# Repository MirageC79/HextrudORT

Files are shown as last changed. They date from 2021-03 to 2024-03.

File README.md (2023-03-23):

# HextrudORT
Light, small and efficient extruder based on the popular Bondtech BMG.
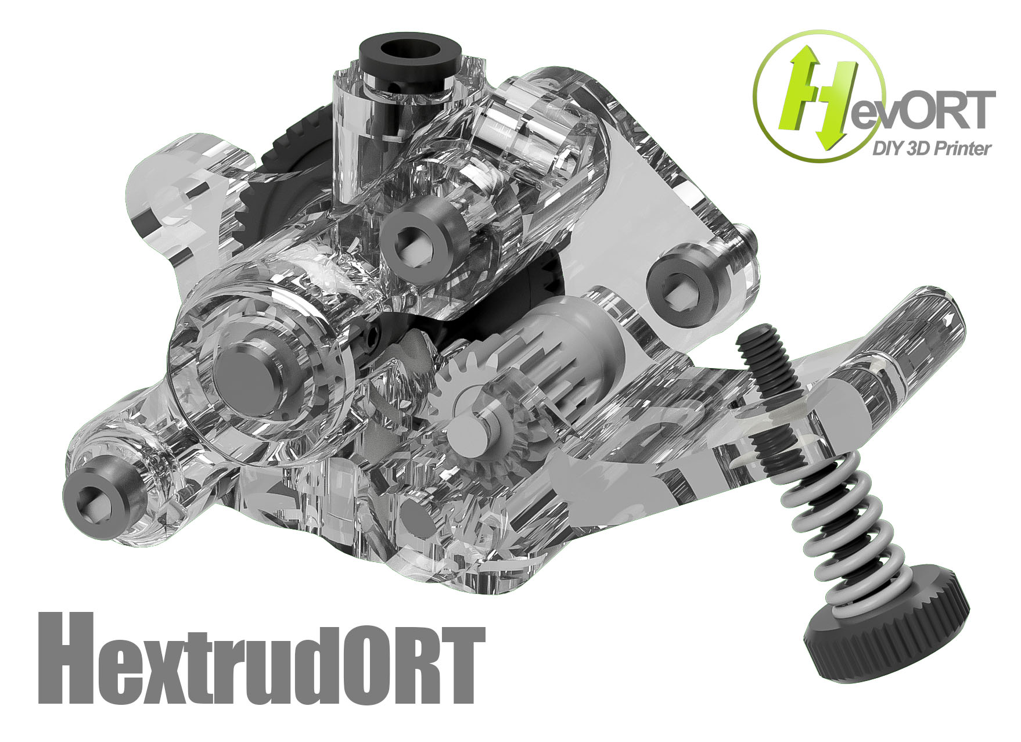
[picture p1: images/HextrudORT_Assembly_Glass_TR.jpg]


## Why the HextrudORT:
The HextrudORT is the simple combination of a proven concept and the desire to obtain a compact and lightweight print head for fast 3D printing.  
Re-using the internal components from the popular and efficient [Bondtech BMG](https://www.bondtech.se/en/product/bmg-extruder/){:target="_blank"}, this extruder was specifically designed to be merged into the [HevORT's](www.hevort.com) print head carriage.

<br>
<br>
<iframe width="200" height="150" src="https://www.youtube.com/embed/5HKC9tRqtTw" frameborder="0" allow="accelerometer; autoplay; clipboard-write; encrypted-media; gyroscope; picture-in-picture" allowfullscreen></iframe> <iframe width="200" height="150" src="https://www.youtube.com/embed/h-ukClHtai4" title="YouTube video player" frameborder="0" allow="accelerometer; autoplay; clipboard-write; encrypted-media; gyroscope; picture-in-picture" allowfullscreen></iframe> <iframe width="200" height="150" src="https://www.youtube.com/embed/YIFRRQczDmg" frameborder="0" allow="accelerometer; autoplay; clipboard-write; encrypted-media; gyroscope; picture-in-picture" allowfullscreen></iframe>

<br>

<br>
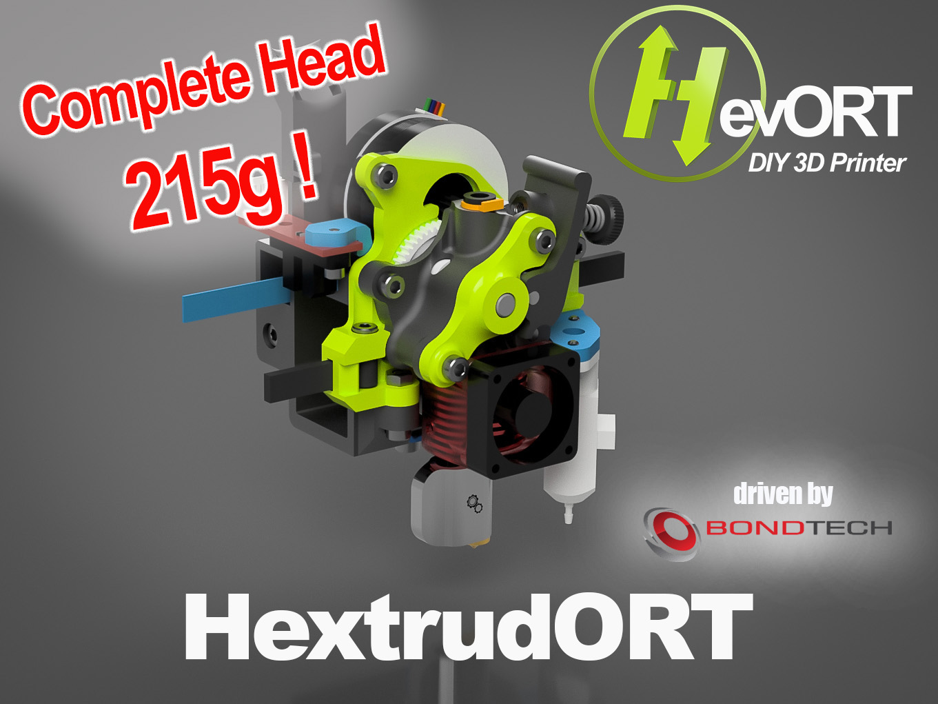
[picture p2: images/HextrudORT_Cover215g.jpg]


### Modular approach!
Several configurations can be created to support all HevORT XY gantry types as well as many populat HotEnds.  Select from the two tables here below your desired configuration and assemble them together :) 

### Change log: 
[Check here for change history:](https://github.com/MirageC79/HextrudORT/releases)

## Carriages

Item<br>Click for CAD|HevORT XY gantry to be used with|Data|Release Status
---------------------|--------------------------------|---|:------------:
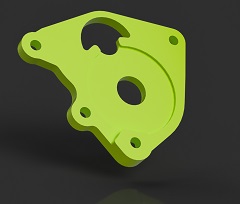
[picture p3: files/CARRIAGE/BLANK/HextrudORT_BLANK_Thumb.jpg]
Blank (https://a360.co/3tu2M2F)
{:target="_blank"}|*This is up to your imagination*|[STLs](https://www.thingiverse.com/thing:4796948){:target="_blank"} <br> <br> Merge this plate to your CAD in order install the Hextrudort|**RELEASED March 2021**
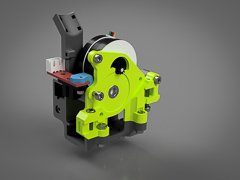
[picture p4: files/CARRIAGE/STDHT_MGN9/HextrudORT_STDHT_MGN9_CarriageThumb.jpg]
STDHTMGN9 (https://a360.co/3bJBDmp)
{:target="_blank"}|STD/HT MGN9|[STLs](https://www.thingiverse.com/thing:4793215){:target="_blank"} <br> <br> [BOM & Notes](/files/CARRIAGE/STDHT_MGN9/BOM_HextrudORT_Carriage_STDHT_MGN9.htm){:target="_blank"} <br> <br> [Excel](/files/CARRIAGE/STDHT_MGN9/BOM_HextrudORT_Carriage_STDHT_MGN9.xlsx)|**RELEASED March 2021**
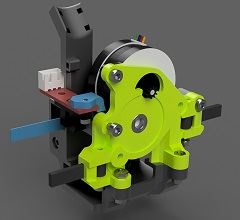
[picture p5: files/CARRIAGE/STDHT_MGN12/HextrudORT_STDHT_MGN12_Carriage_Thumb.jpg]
STDHTMGN12 (https://a360.co/3m0Uj4F)
{:target="_blank"}|STD/HT MGN12|[STLs](https://www.thingiverse.com/thing:4810748){:target="_blank"} <br> <br> [BOM & Notes](/files/CARRIAGE/STDHT_MGN12/BOM_HextrudORT_Carriage_STDHT_MGN12.htm){:target="_blank"} <br> <br> [Excel](/files/CARRIAGE/STDHT_MGN12/BOM_HextrudORT_Carriage_STDHT_MGN12.xlsx)|**RELEASED March 2021**
To come...|HD9|...|*est. April 2021*
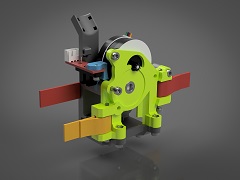
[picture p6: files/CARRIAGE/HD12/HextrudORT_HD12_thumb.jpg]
HD12 (https://a360.co/3bAL0EV)
{:target="_blank"}|HD12(MGN12)|[STLs](https://www.thingiverse.com/thing:4790412){:target="_blank"} <br> <br> [BOM & Notes](/files/CARRIAGE/HD12/BOM_HextrudORT_Carriage_HD12.htm){:target="_blank"} <br> <br> [Excel](/files/CARRIAGE/HD12/BOM_HextrudORT_Carriage_HD12.xlsx)|**RELEASED March 2021**

## Extruder & HotEnds Configs

Item<br>Click for CAD|HotEnd|Data|Release Status
---------------------|------|----|:------------:
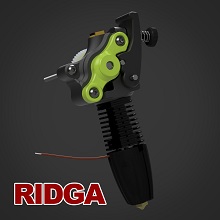
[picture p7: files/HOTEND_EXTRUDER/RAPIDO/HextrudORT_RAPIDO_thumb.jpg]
RAPIDO HotEnd (https://a360.co/3JzDvPC)
{:target="_blank"}|[RAPIDO & RAPIDO UHF](https://www.phaetus.com/rapido-plus/)|[STLs](https://github.com/MirageC79/HextrudORT/tree/main/files/HOTEND_EXTRUDER/RAPIDO/STLs){:target="_blank"} <br> <br> [BOM & Notes](/files/HOTEND_EXTRUDER/RAPIDO/BOM_HextrudORT_Extruder_Rapido.htm){:target="_blank"} <br> <br> [Excel](/files/HOTEND_EXTRUDER/RAPIDO/BOM_HextrudORT_Extruder_Rapido.xlsx)|**V1.65 March 2023**
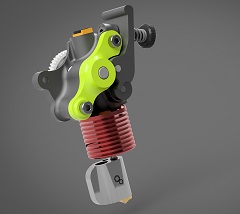
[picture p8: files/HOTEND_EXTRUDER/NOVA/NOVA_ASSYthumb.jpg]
NovaHotEnd (https://a360.co/3cmE7WT)
|[Nova HotEnd](https://3dpassion.com/nova)|[STLs](https://www.thingiverse.com/thing:4790773){:target="_blank"} <br> <br> [BOM & Notes](/files/HOTEND_EXTRUDER/NOVA/BOM_HextrudORT_Extruder_NOVA.htm){:target="_blank"} <br> <br> [Excel](/files/HOTEND_EXTRUDER/NOVA/BOM_HextrudORT_Extruder_NOVA.xlsx)|**RELEASED March 2021**
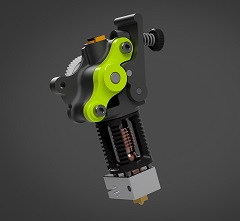
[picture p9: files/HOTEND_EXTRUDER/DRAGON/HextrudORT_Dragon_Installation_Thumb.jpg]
Dragon (https://a360.co/3tqIMhf)
{:target="_blank"}|[Dragon HotEnd](https://s.click.aliexpress.com/e/_AD0Qow)|[STLs](https://www.thingiverse.com/thing:4796562){:target="_blank"} <br> <br> [BOM & Notes](/files/HOTEND_EXTRUDER/DRAGON/BOM_HextrudORT_Extruder_Dragon.htm){:target="_blank"} <br> <br> [Excel](/files/HOTEND_EXTRUDER/DRAGON/BOM_HextrudORT_Extruder_Dragon.xlsx)|**RELEASED March 2021**
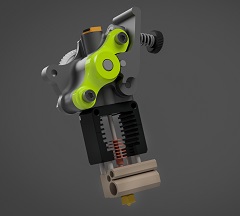
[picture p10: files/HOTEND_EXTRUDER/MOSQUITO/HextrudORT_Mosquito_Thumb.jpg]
Mosquito (https://a360.co/3tJ0A8Q)
{:target="_blank"}|[Mosquito HotEnd](https://www.sliceengineering.com/collections/mosquito-the-professional-hotend)|[STLs](https://www.thingiverse.com/thing:4965960){:target="_blank"} <br> <br> [BOM & Notes](/files/HOTEND_EXTRUDER/MOSQUITO/BOM_HextrudORT_Extruder_Mosquito.htm){:target="_blank"} <br> <br> [Excel](/files/HOTEND_EXTRUDER/MOSQUITO/BOM_HextrudORT_Extruder_Mosquito.xlsx)|**RELEASED September 2021**
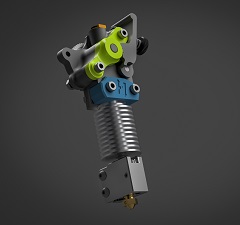
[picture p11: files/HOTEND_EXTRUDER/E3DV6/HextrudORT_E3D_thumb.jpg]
E3D V6 & Volcano (https://a360.co/3dGhSNx)
{:target="_blank"}|[E3D V6 & Volcano HotEnd](https://e3d-online.com/)|[STLs](https://www.thingiverse.com/thing:4971939){:target="_blank"} <br> <br> [BOM & Notes](/files/HOTEND_EXTRUDER/E3DV6/BOM_HextrudORT_Extruder_E3D.htm){:target="_blank"} <br> <br> [Excel](/files/HOTEND_EXTRUDER/E3DV6/BOM_HextrudORT_Extruder_E3D.xlsx)|**RELEASED September 2021**

<br>

## Report Issues [HERE](https://github.com/MirageC79/HextrudORT/issues)

<br>

## Back to [HevORT project](https://www.hevort.com)

<br>

**If you like my work** and would like to help me covering the costs associated to the development and improvement of this project, <br>
click the button here below :)

<form action="https://www.paypal.com/cgi-bin/webscr" method="post" target="_top">
<input type="hidden" name="cmd" value="_s-xclick" />
<input type="hidden" name="hosted_button_id" value="LYP98YKUSLXN2" />
<input type="image" src="https://www.paypalobjects.com/en_US/i/btn/btn_donateCC_LG.gif" border="0" name="submit" title="PayPal - The safer, easier way to pay online!" alt="Donate with PayPal button" />

</form>

Thank you!
Olivier

FB (https://www.facebook.com/groups/hevort) FaceBook Group <br>
forum (https://forums.hevort.com/index.php)  Discussion Forum <br>
Discord (https://discord.gg/WgZMrFSp) Discord Server <br>

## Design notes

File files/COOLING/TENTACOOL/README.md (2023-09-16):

# TentaCool
*design by sillisam71  
idea by MirageC*

## What if we are using CPAP turbine wrong?
I mean this thing is capable of decent pressure levels while still moving great amount of air...
And yet we are designing ducts with as little restriction as possible in order to get the maximum flow to the output nozzles.  

## Hypothesis:
Would an hybrid between berdair and regular ducting be something that would be better suited for that monster turbine?  More turbulent flow, more output holes and diffusers... see my point...   
What if we could create a carpet of turbulent air around the last layer?

TentaCool Pressure testing (https://www.youtube.com/watch?v=26Ztry5WomM)

Special thanks to *sillysam71* from the [HevORT discord server](https://discord.gg/4kxH2He3ab)  for this AMAZING creation based on my unclear and foggy explanations...
<br>
<br>

## Compatibility
- HextrudORT HD12 MGN9
  - Volcano
  - Rapido
  - Rapido UHF
  - CHC Volcano
- VZ PrintHead for HevORT (All HDs)
  - Goliath Short (Watercooled Extruder)
  - Pretty much any other hotend
    
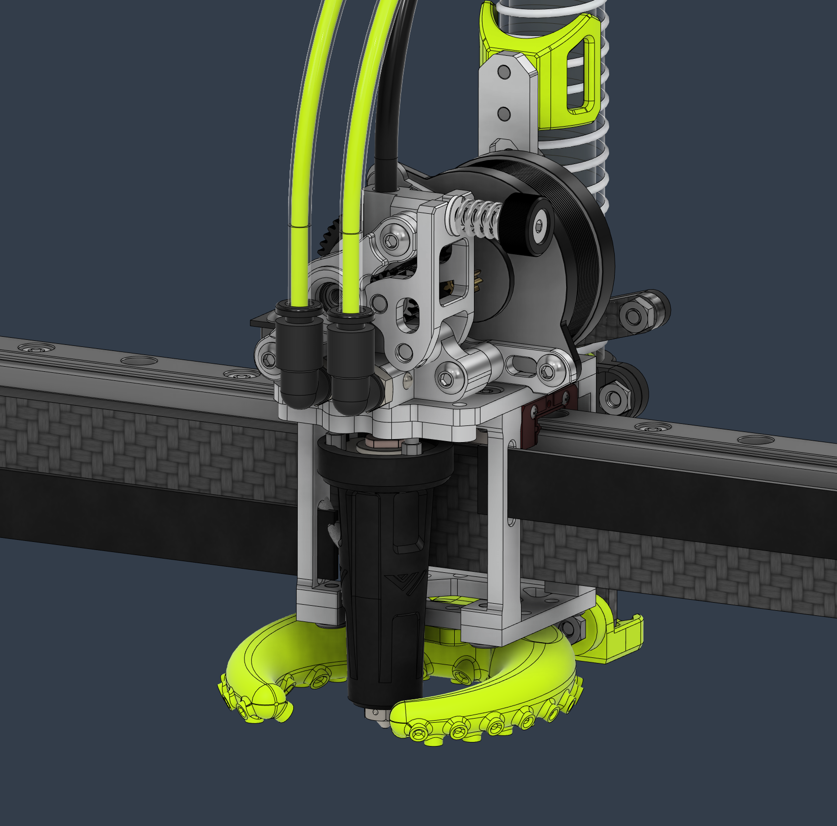
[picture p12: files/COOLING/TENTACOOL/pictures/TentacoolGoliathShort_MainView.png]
TentaCool VzPrintHead Goliath Short

tentacool_HD12_MGN9 Install
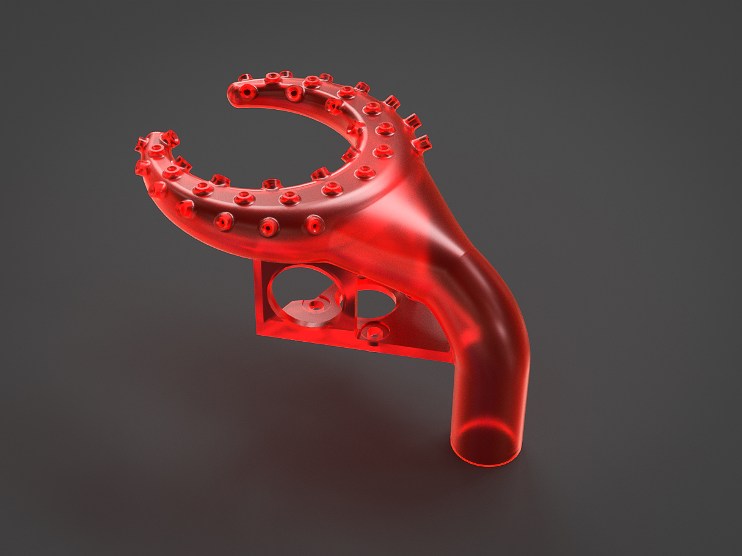
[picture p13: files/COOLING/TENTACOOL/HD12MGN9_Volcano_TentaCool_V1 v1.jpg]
TentaCool Duct


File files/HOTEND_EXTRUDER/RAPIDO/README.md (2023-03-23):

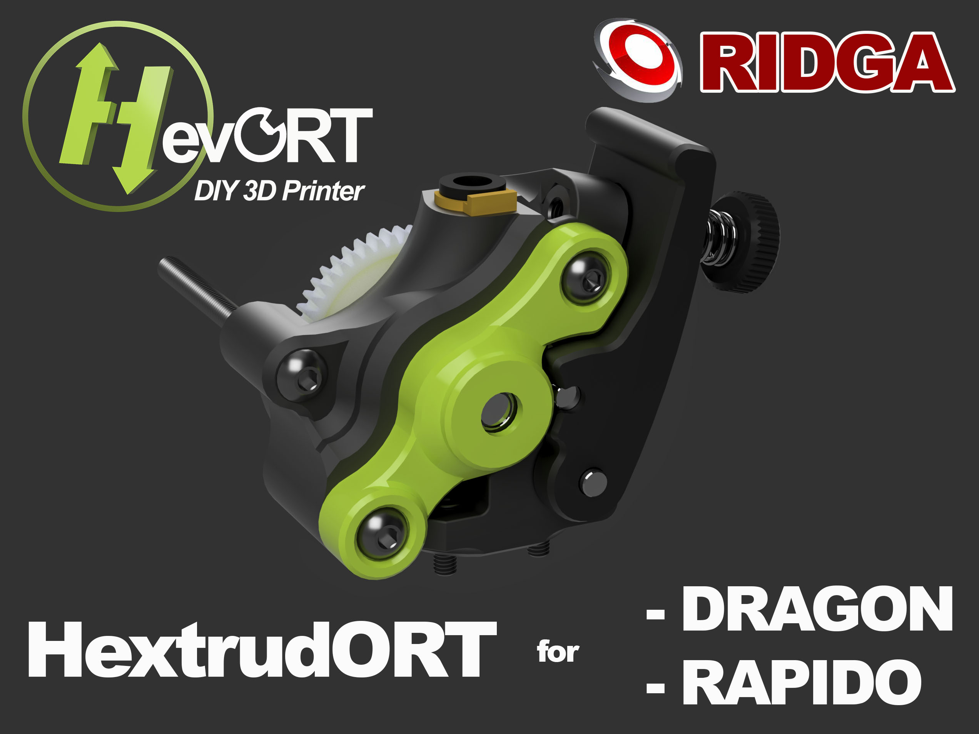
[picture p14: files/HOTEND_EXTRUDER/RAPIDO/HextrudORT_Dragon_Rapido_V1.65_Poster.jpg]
rapido


# [- CAD](https://a360.co/3JzDvPC) #
# [- BOM](https://miragec79.github.io/HextrudORT/files/HOTEND_EXTRUDER/RAPIDO/BOM_HextrudORT_Extruder_Rapido.htm) #

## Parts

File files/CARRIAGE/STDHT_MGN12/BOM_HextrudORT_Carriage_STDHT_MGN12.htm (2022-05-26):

SubAssy | Category | Item | Thumbnail | Part Name | Part Description | Make/Buy | QTY | Comment | Vendor | Vendor URL
HextrudORT Carriage_STDHT_MGN9 | BUY | 1
HextrudORT Carriage_STDHT_MGN9 | BUY | 1
HextrudORT Carriage_STDHT_MGN9 | BUY | 2
HextrudORT Carriage_STDHT_MGN9 | BUY | 3
HextrudORT Carriage_STDHT_MGN9 | HARDWARE | 4
HextrudORT Carriage_STDHT_MGN9 | HARDWARE | 6
HextrudORT Carriage_STDHT_MGN9 | HARDWARE | 17
HextrudORT Carriage_STDHT_MGN9 | HARDWARE | 18
HextrudORT Carriage_STDHT_MGN9 | HARDWARE | 19
HextrudORT Carriage_STDHT_MGN9 | HARDWARE | 20
HextrudORT Carriage_STDHT_MGN9 | HARDWARE | 21
HextrudORT Carriage_STDHT_MGN9 | HARDWARE | 22
HextrudORT Carriage_STDHT_MGN9 | HARDWARE | 23
HextrudORT Carriage_STDHT_MGN9 | MAKE | 27
HextrudORT Carriage_STDHT_MGN9 | MAKE | 28
HextrudORT Carriage_STDHT_MGN9 | MAKE | 29
HextrudORT Carriage_STDHT_MGN9 | MAKE | 30

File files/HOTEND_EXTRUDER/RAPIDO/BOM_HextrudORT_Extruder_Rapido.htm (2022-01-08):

SubAssy | Category | Item | Thumbnail | Part Name | Part Description | Make/Buy | QTY | Comment | Vendor | Vendor URL
Bondtech BMG parts
HextrudORT_HotEnd_RAPIDO | BUY | 1
HextrudORT_HotEnd_RAPIDO | BUY | 2
HextrudORT_HotEnd_RAPIDO | BUY | 3
HextrudORT_HotEnd_RAPIDO | BUY | 4
HextrudORT_HotEnd_RAPIDO | BUY | 5
HextrudORT_HotEnd_RAPIDO | BUY | 6a
Dragon HextrudORT
HextrudORT_HotEnd_RAPIDO | BUY | 6b
HextrudORT_HotEnd_RAPIDO | BUY | 7
HextrudORT_HotEnd_RAPIDO | MAKE | 8
HextrudORT_HotEnd_RAPIDO | BUY | 9a
HextrudORT_HotEnd_RAPIDO | BUY | 9b
HextrudORT_HotEnd_RAPIDO | BUY | 10
HextrudORT_HotEnd_RAPIDO | HARDWARE | 11
HextrudORT_HotEnd_RAPIDO | HARDWARE | 12
HextrudORT_HotEnd_RAPIDO | HARDWARE | 13
HextrudORT_HotEnd_RAPIDO | HARDWARE | 14
HextrudORT_HotEnd_RAPIDO | HARDWARE | 15
STD/HT
HextrudORT_HotEnd_RAPIDO | MAKE | 10a | To come | BlTouchSupport for STDHT MGN9 & MGN12 Carriage | 3D Printed | MAKE | 1* | * OPTION BlTouchSupport for STDHT MGN9 & MGN12 Carriage | Not Ready
HD9
HextrudORT_HotEnd_RAPIDO | MAKE | 10b | To come | BLTouch support for HD9 | 3D Printed | MAKE | 1* | * OPTION BlTouchSupport for HD9 Carriage | Not Ready
HD12
HextrudORT_HotEnd_RAPIDO | MAKE(Option*) | 10C1
HextrudORT_HotEnd_RAPIDO | MAKE(Option*) | 10C2
HextrudORT_HotEnd_RAPIDO | MAKE(Option*) | 11a
HextrudORT_HotEnd_RAPIDO | MAKE(Option*) | 12a | HORTPC_RapidoUHF_Spacer HD12_MGN9 | 3D Printed |  | 1* | RAPIDO UHF spacer for HORTPC HevORT Remote Turbine Part Cooling *For HD12_MGN9 |  | https://www.thingiverse.com/thing:5173653
HextrudORT_HotEnd_RAPIDO | MAKE(Option*) | 13a
HextrudORT_HotEnd_RAPIDO | MAKE(Option*) | 11b
HextrudORT_HotEnd_RAPIDO | MAKE(Option*) | 12b
HextrudORT_HotEnd_RAPIDO | MAKE(Option*) | 13b
HextrudORT RAPIDO
HextrudORT_HotEnd_RAPIDO | MAKE | 14
HextrudORT_HotEnd_RAPIDO | MAKE | 15
HextrudORT_HotEnd_RAPIDO | MAKE | 16
HextrudORT_HotEnd_RAPIDO | MAKE(Option) | 11C

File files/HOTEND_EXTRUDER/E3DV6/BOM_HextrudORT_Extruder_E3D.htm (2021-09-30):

SubAssy | Category | Item | Thumbnail | Part Name | Part Description | Make/Buy | QTY | Comment | Vendor | Vendor URL
Bondtech BMG parts
HextrudORT_HotEnd_E3D | BUY | 1
HextrudORT_HotEnd_E3D | BUY | 2
HextrudORT_HotEnd_E3D | BUY | 3
HextrudORT_HotEnd_E3D | BUY | 4
HextrudORT_HotEnd_E3D | BUY | 5
HextrudORT_HotEnd_E3D | BUY | 6a
E3D V6 HextrudORT
HextrudORT_HotEnd_E3D | BUY | 6b
HextrudORT_HotEnd_E3D | MAKE | 7
HextrudORT_HotEnd_E3D | BUY | 8
OptionA - E3DV6
HextrudORT_HotEnd_E3D | BUY | 9 - Option A
HextrudORT_HotEnd_E3D | MAKE | 10(A1)
HextrudORT_HotEnd_E3D | MAKE | 10(A2)
HextrudORT_HotEnd_E3D | MAKE | 10(A3)
HextrudORT_HotEnd_E3D | MAKE | 10(A4) | To Come | Volcano BLTouch support for HD9 | 3D Printed | MAKE | 1* | Not Available Yet * Select BlTouch Bracket to fit your selected HextrudORT carriage.
OptionB- E3DVolcano
HextrudORT_HotEnd_E3D | BUY | 9 - Option B
HextrudORT_HotEnd_E3D | MAKE | 10(B1)
HextrudORT_HotEnd_E3D | MAKE | 10(B2)
HextrudORT_HotEnd_E3D | MAKE | 10(B3)
HextrudORT_HotEnd_E3D | MAKE | 10(B4) | To come | Volcano BLTouch support for HD9 | 3D Printed | MAKE | 1* | Not Available Yet * Select BlTouch Bracket to fit your selected HextrudORT carriage.
HextrudORT_HotEnd_E3D | BUY | 10
HextrudORT_HotEnd_E3D | HARDWARE | 11
HextrudORT_HotEnd_E3D | HARDWARE | 13
HextrudORT_HotEnd_E3D | HARDWARE | 14
HextrudORT_HotEnd_E3D | HARDWARE | 15
HextrudORT_HotEnd_E3D | MAKE | 16
HextrudORT_HotEnd_E3D | MAKE | 17
HextrudORT_HotEnd_E3D | MAKE | 18
HextrudORT_HotEnd_E3D | MAKE | 19

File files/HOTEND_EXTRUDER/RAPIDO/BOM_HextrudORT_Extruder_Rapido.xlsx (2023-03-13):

 |  |  |  | LINK TO CAD (https://a360.co/3JzDvPC) | V1.65 integrates a few changes to accept the new RIDGA gear from Bondtech as well as some enhancements to the overal rigidity of the unit.
SubAssy | Category | Item | Thumbnail | Part Name | Part Description | Make/Buy | QTY | Comment | Vendor | Vendor URL
Bondtech RIDGA HextrudORT Kit
HextrudORT_HotEnd_RAPIDO | BUY | 1 |  | 1.75/5.0mm BMG Secondary Drive Gear | Included in BMG Internals Set for HextrudORT | (BUY) KIT | 1 |  | Bondtech | Reverse BMG Set for HextrudORT from the HevORT project (bondtech.se) (https://www.bondtech.se/product/bmg-reverse-set-for-hextrudort/)
HextrudORT_HotEnd_RAPIDO | BUY | 2 |  | R.I.D.G.A. – BMG Reverse Integrated Drive Gear Assembly | Included in BMG Internals Set for HextrudORT | (BUY) KIT | 1 |  | Bondtech | Reverse BMG Set for HextrudORT from the HevORT project (bondtech.se) (https://www.bondtech.se/product/bmg-reverse-set-for-hextrudort/)
HextrudORT_HotEnd_RAPIDO | BUY | 3 |  | Thumbscrew Assembly | Included in BMG Internals Set for HextrudORT | (BUY) KIT | 1 |  | Bondtech | Reverse BMG Set for HextrudORT from the HevORT project (bondtech.se)
HextrudORT_HotEnd_RAPIDO | BUY | 4 |  | TensionArm Pin 3 X 20mm | Included in BMG Internals Set for HextrudORT | (BUY) KIT | 1 |  | Bondtech | Reverse BMG Set for HextrudORT from the HevORT project (bondtech.se)
HextrudORT_HotEnd_RAPIDO | BUY | 5 |  | PTFE Tube Retainer | Included in BMG Internals Set for HextrudORT | (BUY) KIT | 1 |  | Bondtech | Reverse BMG Set for HextrudORT from the HevORT project (bondtech.se)
HextrudORT_HotEnd_RAPIDO | BUY | 6 |  | MR84 8X4X3 Bearing | Included in BMG Internals Set for HextrudORT | (BUY) KIT | 2 |  | Bondtech | Reverse BMG Set for HextrudORT from the HevORT project (bondtech.se)
Dragon HextrudORT
HextrudORT_HotEnd_RAPIDO | BUY | 7 |  | bltouch |  | BUY | 1
HextrudORT_HotEnd_RAPIDO | MAKE | 8 |  | PTFE_Guide | Comes with BMG clones | MAKE | 1 | Make from 4mm OD PTFE tube: 1 - Using Xacto blade, create internal chamfer in one end. 2 - Cut that end into an arrow shape (try to match the angle from the HextrudORT body where the hobb gears meet. 3 - Insert into HextrudORT body and cut excess length flush.
HextrudORT_HotEnd_RAPIDO | BUY | 9a |  | RAPIDO HOTEND | Standard | BUY | 1 | Phaetus Rapido Hot End | Phaetus: https://www.phaetus.com/rapido-hotend/ Aliexpress | https://s.click.aliexpress.com/e/_9xIrem
HextrudORT_HotEnd_RAPIDO | BUY | 9b |  | RAPIDO HOTEND UHF | Ultra High Flow - with melt zone extender | BUY | 1 | This version adds a small 8.5mm longg extender to the meltzone, making possible the use of E3D Volcano nozzles | Phaetus: https://www.phaetus.com/rapido-hotend/ Aliexpress | https://s.click.aliexpress.com/e/_9xIrem
HextrudORT_HotEnd_RAPIDO | BUY | 10 |  | 2510 Fan - 25mm*10mm | 2510 fan | BUY | 2 |  | Aliexpress | https://s.click.aliexpress.com/e/_9wYbbC
HextrudORT_HotEnd_RAPIDO | HARDWARE | 11 |  | M2.5X8_ 90358A112_Ultra-Low-Profile Socket Head Screw | Screw, Capr_M2.5 X 8mm | Buy | 3 | *Ultra low head screws are used to increase available material thickness holding hotend. | Aliexpress | https://s.click.aliexpress.com/e/_DEoG91j
HextrudORT_HotEnd_RAPIDO | HARDWARE | 12 |  | M3_Nut_94150A325 | Nut, Hex - M3 | Buy | 2
HextrudORT_HotEnd_RAPIDO | HARDWARE | 13 |  | M3X40_CapScrew_92290A128 | Screw, Cap - M3X40mm | Buy | 1 | Button Head screw can be used as well.
HextrudORT_HotEnd_RAPIDO | HARDWARE | 14 |  | M3X25_CapScrew_92290A124 | Screw, Cap - M3X25mm | Buy | 1 | Button Head screw can be used as well.
HextrudORT_HotEnd_RAPIDO | HARDWARE | 15 |  | M3X20_CapScrew_92290A122 | Screw, Cap - M3X20mm | Buy | 1 | Button Head screw can be used as well.
HextrudORT_HotEnd_RAPIDO | HARDWARE | 16 |  | M3X8_CapScrew_92290A113 | Screw, Cap - M3X8mm | Buy | 1 | Button Head screw can be used as well.
STD/HT
HextrudORT_HotEnd_RAPIDO | MAKE | 17a | To come | BlTouchSupport for STDHT MGN9 & MGN12 Carriage | 3D Printed | MAKE | 1* | * OPTION BlTouchSupport for STDHT MGN9 & MGN12 Carriage | Not Ready
HextrudORT_HotEnd_RAPIDO | MAKE | 18d |  | HextrudORT_STDHT_MGN9_RapidoUHF_StructFanShroud_25mm_BLTouch v1.stl | 3D Printed | MAKE | 1* | *OPTION Allows the mounting of Bltouch directly onto the FanShroud | Github | HextrudORT/files/HOTEND_EXTRUDER/RAPIDO/STLs at main · MirageC79/HextrudORT (github.com) (https://github.com/MirageC79/HextrudORT/tree/main/files/HOTEND_EXTRUDER/RAPIDO/STLs)
HD9
HextrudORT_HotEnd_RAPIDO | MAKE | 17b | To come | BLTouch support for HD9 | 3D Printed | MAKE | 1* | * OPTION BlTouchSupport for HD9 Carriage | Not Ready
HD12
HextrudORT_HotEnd_RAPIDO | MAKE(Option*) | 17c1 |  | BLTouch support for HD12 RAPIDO | 3D Printed | MAKE | 1* | *For HextrudORT HD12 Rapido standard. |  | HextrudORT/files/HOTEND_EXTRUDER/RAPIDO/STLs at main · MirageC79/HextrudORT (github.com) (https://github.com/MirageC79/HextrudORT/tree/main/files/HOTEND_EXTRUDER/RAPIDO/STLs)
HextrudORT_HotEnd_RAPIDO | MAKE(Option*) | 17c2 |  | BLTouch support for HD12 RAPIDO UHF | 3D Printed | MAKE | 1* | *For HextrudORT HD12 Rapido UHF (Ultra High Flow) |  | HextrudORT/files/HOTEND_EXTRUDER/RAPIDO/STLs at main · MirageC79/HextrudORT (github.com)
HextrudORT_HotEnd_RAPIDO | MAKE(Option*) | 18b |  | Rapido Structural Fan Mount HD12 MGN9 | 3D Printed | MAKE | 1* | For HextrudORT HD12 Rapido Standard and High Flow. This fan shroud acts as an additional mouting point for the RAPIDO hotend. *For HD12_MGN9 |  | HextrudORT/files/HOTEND_EXTRUDER/RAPIDO/STLs at main · MirageC79/HextrudORT (github.com)
HextrudORT_HotEnd_RAPIDO | MAKE(Option*) | 19b |  | HORTPC_RapidoUHF_Spacer HD12_MGN9 | 3D Printed | MAKE | 1* | RAPIDO UHF spacer for HORTPC HevORT Remote Turbine Part Cooling *For HD12_MGN9 |  | HextrudORT/files/HOTEND_EXTRUDER/RAPIDO/STLs at main · MirageC79/HextrudORT (github.com)
HextrudORT_HotEnd_RAPIDO | MAKE(Option*) | 20b |  | HORTPC_Rapido_HD12_MGN9 | 3D Printed (Resin)** | MAKE | 1* | HD12 MGN9 Rapido HORTPC - HevORT Remote Turbine Part Cooling **Recommended to be printed from SLA (Resin Printer) *For HD12_MGN9 |  | HextrudORT/files/HOTEND_EXTRUDER/RAPIDO/STLs at main · MirageC79/HextrudORT (github.com)
HextrudORT_HotEnd_RAPIDO | MAKE(Option*) | 18c |  | Rapido Structural Fan Mount HD12_MGN12 | 3D Printed | MAKE | 1* | For HextrudORT HD12 Rapido Standard and High Flow. This fan shroud acts as an additional mouting point for the RAPIDO hotend. *For HD12_MGN12 | USER MOD!! Thanks to DonnerPlays from HevORT Discord channel | HextrudORT/files/HOTEND_EXTRUDER/RAPIDO/STLs at main · MirageC79/HextrudORT (github.com)
HextrudORT_HotEnd_RAPIDO | MAKE(Option*) | 19c |  | HORTPC_RapidoUHF_Spacer HD12_MGN12 | 3D Printed | MAKE | 1* | RAPIDO UHF spacer for HORTPC HevORT Remote Turbine Part Cooling *For HD12_MGN12 | USER MOD!! Thanks to DonnerPlays from HevORT Discord channel | HextrudORT/files/HOTEND_EXTRUDER/RAPIDO/STLs at main · MirageC79/HextrudORT (github.com)
HextrudORT_HotEnd_RAPIDO | MAKE(Option*) | 20c |  | HORTPC_Rapido HD12_MGN12 | 3D Printed (Resin)** | MAKE | 1* | HD12 MGN9 Rapido HORTPC - HevORT Remote Turbine Part Cooling **Recommended to be printed from SLA (Resin Printer) *For HD12_MGN12 | USER MOD!! Thanks to DonnerPlays from HevORT Discord channel | HextrudORT/files/HOTEND_EXTRUDER/RAPIDO/STLs at main · MirageC79/HextrudORT (github.com) (https://github.com/MirageC79/HextrudORT/tree/main/files/HOTEND_EXTRUDER/RAPIDO/STLs)
HextrudORT RAPIDO
HextrudORT_HotEnd_RAPIDO | MAKE(Option) | 18a |  | Rapido Fan Shroud | 3D Printed | MAKE | 1* | Standard fan shroud for Rapido by MirageC |  | HextrudORT/files/HOTEND_EXTRUDER/RAPIDO/STLs at main · MirageC79/HextrudORT (github.com)
HextrudORT_HotEnd_RAPIDO | MAKE | 21 |  | HextrudORT_Dragon_TENSION_ARM_body_V1.6_RIDGA | 3D_Printed | MAKE | 1 | Note: you can find pre-supported STL in the github repository: HextrudORT_Dragon_TENSION_ARM_body_V1.6_RIDGA_Supported.stl |  | HextrudORT/files/HOTEND_EXTRUDER/RAPIDO/STLs at main · MirageC79/HextrudORT (github.com) (https://github.com/MirageC79/HextrudORT/tree/main/files/HOTEND_EXTRUDER/RAPIDO/STLs)
HextrudORT_HotEnd_RAPIDO | MAKE | 22 |  | HextrudORT_COVER_MR84_V1.65_RIDGA | 3D_Printed | MAKE | 1 |  |  | HextrudORT/files/HOTEND_EXTRUDER/RAPIDO/STLs at main · MirageC79/HextrudORT (github.com)
HextrudORT_HotEnd_RAPIDO | MAKE | 23 |  | HextrudORT_Dragon_Rapido_body_V1.65_RIDGA | 3D Printed | MAKE | 1 | NOTE ! Make sure your printer is well calibrated, these are small and precise parts. Recommended print settings: - 0.16 Layer height - Support interface: yes - Full fan at first support interfacing layer you can find pre-supported STL in the github repository: HextrudORT_Dragon_Rapido_body_V1.6_RIDGA_Supported.stl |  | HextrudORT/files/HOTEND_EXTRUDER/RAPIDO/STLs at main · MirageC79/HextrudORT (github.com) (https://github.com/MirageC79/HextrudORT/tree/main/files/HOTEND_EXTRUDER/RAPIDO/STLs)

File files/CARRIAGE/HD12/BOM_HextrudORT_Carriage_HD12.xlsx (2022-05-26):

SubAssy | Category | Item | Thumbnail | Part Name | Part Description | Make/Buy | QTY | Comment | Vendor | Vendor URL
HextrudORT_Carriage_HD12 | BUY | 1 |  | NEMA_LDO_36STH17-1004AHG v6 |  |  | 1 | WARNING!! DO NOT SET CURRENT HIGHER THAN 0.400ma in your printer config file. These motors are Class H and are rated for 180C, they can become VERY HOT and might melt your carriage Spec: https://miragec79.github.io/HextrudORT/docs/LDO-36STH17-1004AHG-RevA_1.pdf Important Note: ref: https://github.com/MirageC79/HextrudORT/issues/9 Depending on source of components, printing tolerances and the fact that the design clearances are reduced to a minimal, you may need to file/trim a section of the Nema 14 motor to clear the XY cross member. This modifcation will not affect motor performance or reliability.
HextrudORT_Carriage_HD12 | BUY | 2 |  | Opto endstop PM | Optical End-Stop | Buy | 1
HextrudORT_Carriage_HD12 | HARDWARE | 4 |  | M3_Nut_94150A325 | Nut, Hex - M3 | Buy | 5
HextrudORT_Carriage_HD12 | HARDWARE | 5 |  | M2.5X8_CapScrew_92290A058 | Screwm Cap_M2.5 X 8mm | Buy | 1
HextrudORT_Carriage_HD12 | HARDWARE | 6 |  | M3X6_CapScrew_92290A111 | Screw, Cap - M3X6mm | Buy | 5
HextrudORT_Carriage_HD12 | HARDWARE | 7 |  | M3X12_CapScrew_92290A117 | Screw, Cap - M3X12mm | Buy | 2
HextrudORT_Carriage_HD12 | HARDWARE | 8 |  | M3X14_CapScrew_92290A118 | Screw, Cap - M3X14 | Buy | 1
HextrudORT_Carriage_HD12 | HARDWARE | 9 |  | M3X25_CapScrew_92290A124 | Screw, Cap - M3X25mm | Buy | 1
HextrudORT_Carriage_HD12 | HARDWARE | 10 |  | M3X30_CapScrew_92290A126 | Screw, Cap - M3X30mm | Buy | 2
HextrudORT_Carriage_HD12 | HARDWARE | 11 |  | M4X40_CapScrew_91290A174 | Screw, Cap - M4X40mm | Buy | 1
HextrudORT_Carriage_HD12 | MAKE | 12 |  | HextrudORT_HD12_CarriageBAckPlate_Body OR HextrudORT_HD12_CarriageBAckPlate_Body_BB | 3D Printed | Make | 1 | NOTE ! For Big Bearings (MR95 5X9X2.5) use: HextrudORT_HD12_CarriageBAckPlate_Body_BB.stl For Bearing provided with BMG (MR85 5x8x2.5) use: HextrudORT_HD12_CarriageBAckPlate_Body.stl | Thingiverse Alternate: GitHub | https://www.thingiverse.com/thing:4790412 alternate: https://github.com/MirageC79/HextrudORT/tree/main/files/CARRIAGE/HD12/STL
HextrudORT_Carriage_HD12 | MAKE | 13 |  | HextrudORT_HD12_Carriage_Body | 3D PRinted | Make | 1 |  | Thingiverse Alternate: GitHub | https://www.thingiverse.com/thing:4790412 alternate: https://github.com/MirageC79/HextrudORT/tree/main/files/CARRIAGE/HD12/STL
HextrudORT_Carriage_HD12 | MAKE | 14 |  | HextrudORT_HD12_OpticalSupport_Body v2 | 3D Printed | Make | 1 |  | Thingiverse Alternate: GitHub | https://www.thingiverse.com/thing:4790412 alternate: https://github.com/MirageC79/HextrudORT/tree/main/files/CARRIAGE/HD12/STL
HextrudORT_Carriage_HD12 | BUY | 3a |  | OPTION B: Bearing_MR85 (from BMG) | Bearing 5X8X2.5 | BUY | 1* | OPTION B Use MR85 5x8x2.5 bearings from BMG
HextrudORT_Carriage_HD12 | BUY | 3b |  | Bearing_MR95_7804K105 | Bearing, 9X5X3 | Buy | 1* | OPTION A These are BIGGER bearings than the ones used in the BMG. To be used with Back Plate and cover marked with "BB"

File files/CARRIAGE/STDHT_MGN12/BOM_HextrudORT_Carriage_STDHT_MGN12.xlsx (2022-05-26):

SubAssy | Category | Item | Thumbnail | Part Name | Part Description | Make/Buy | QTY | Comment | Vendor | Vendor URL
HextrudORT Carriage_STDHT_MGN9 | BUY | 1 |  | LDO_NEMA14_36STH17-1004AHG v6 v2 | LDO NEMA 14 Round | BUY | 1 | WARNING!! DO NOT SET CURRENT HIGHER THAN 0.400ma in your printer config file. These motors are Class H and are rated for 180C, they can become VERY HOT and might melt your carriage Spec: https://miragec79.github.io/HextrudORT/docs/LDO-36STH17-1004AHG-RevA_1.pdf Important Note: ref: https://github.com/MirageC79/HextrudORT/issues/9 Depending on source of components, printing tolerances and the fact that the design clearances are reduced to a minimal, you may need to file/trim a section of the Nema 14 motor to clear the XY cross member. This modifcation will not affect motor performance or reliability.
HextrudORT Carriage_STDHT_MGN9 | BUY | 1 |  | OPTION A: Bearing_MR95_7804K105 | Bearing 5X9X3 | BUY | 2* | OPTION A These are BIGGER bearings than the ones used in the BMG. To be used with Back Plate and cover marked with "BB"
HextrudORT Carriage_STDHT_MGN9 | BUY | 2 |  | OPTION B: Bearing_MR85 (from BMG) | Bearing 5X8X2.5 | BUY | 2* | OPTION B Use MR85 5x8x2.5 bearings from BMG
HextrudORT Carriage_STDHT_MGN9 | BUY | 3 |  | Opto endstop PM | Optical End-Stop | BUY | 1
HextrudORT Carriage_STDHT_MGN9 | HARDWARE | 4 |  | M2.5X8_CapScrew_92290A058 | Screw, Cap_M2.5 X 8mm | BUY | 1
HextrudORT Carriage_STDHT_MGN9 | HARDWARE | 6 |  | M3X6_CapScrew_92290A111 v4 | Screw, Cap - M3X6mm | BUY | 5
HextrudORT Carriage_STDHT_MGN9 | HARDWARE | 17 |  | M3X12_CapScrew_92290A117 | Screw, Cap - M3X12mm | BUY | 2
HextrudORT Carriage_STDHT_MGN9 | HARDWARE | 18 |  | M3X14_CapScrew_92290A118 | Screw, Cap - M3X14 | BUY | 1
HextrudORT Carriage_STDHT_MGN9 | HARDWARE | 19 |  | M3X16_CapScrew_92290A120 | Screw, Cap - M3X16mm | BUY | 1
HextrudORT Carriage_STDHT_MGN9 | HARDWARE | 20 |  | M3X20_CapScrew_92290A122 v3 | Screw, Cap - M3X20mm | BUY | 1
HextrudORT Carriage_STDHT_MGN9 | HARDWARE | 21 |  | M3X25_CapScrew_92290A124 v4 | Screw, Cap - M3X25mm | BUY | 1
HextrudORT Carriage_STDHT_MGN9 | HARDWARE | 22 |  | M3X30_CapScrew_92290A126 | Screw, Cap - M3X30mm | BUY | 2
HextrudORT Carriage_STDHT_MGN9 | HARDWARE | 23 |  | M3_Nut_94150A325 v4 | Nut, Hex - M3 | BUY | 7
HextrudORT Carriage_STDHT_MGN9 | MAKE | 27 |  | CarriageBAckPlate_Body* Or CarriageBAckPlate_Body_BB* | 3D Printed | MAKE | 1 | * NOTE ! For Big Bearings (MR95 5X9X2.5) use: HextrudORT_ BackPlate_STDHT_MGN12_BB.stl For Bearing provided with BMG (MR85 5x8x2.5) use: HextrudORT_ BackPlate_STDHT_MGN12.stl | Thingiverse Alternate: GitHub | https://www.thingiverse.com/thing:4810748 alternate: https://github.com/MirageC79/HextrudORT/tree/main/files/CARRIAGE/STDHT_MGN12/STL
HextrudORT Carriage_STDHT_MGN9 | MAKE | 28 |  | Carriage_Body | 3D PRinted | MAKE | 1 | NOTE ! To be used with MGN9H Rail on X cross member | Thingiverse Alternate: GitHub | https://www.thingiverse.com/thing:4810748 alternate: https://github.com/MirageC79/HextrudORT/tree/main/files/CARRIAGE/STDHT_MGN12/STL
HextrudORT Carriage_STDHT_MGN9 | MAKE | 29 |  | TensionnerBLock | 3D Printed | MAKE | 2 | NOTE ! Make sure your printer is well calibrated, these are small and precise parts. Recommended print settings: - 0.16 Layer height - Support interface: yes - Full fan at first support interfacing layer | Thingiverse Alternate: GitHub | https://www.thingiverse.com/thing:4810748 alternate: https://github.com/MirageC79/HextrudORT/tree/main/files/CARRIAGE/STDHT_MGN12/STL
HextrudORT Carriage_STDHT_MGN9 | MAKE | 30 |  | OpticalSupport_Body | 3D Printed | MAKE | 1 |  | Thingiverse Alternate: GitHub | https://www.thingiverse.com/thing:4810748 alternate: https://github.com/MirageC79/HextrudORT/tree/main/files/CARRIAGE/STDHT_MGN12/STL

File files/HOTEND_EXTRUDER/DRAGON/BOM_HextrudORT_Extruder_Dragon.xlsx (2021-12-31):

SubAssy | Category | Item | Thumbnail | Part Name | Part Description | Make/Buy | QTY | Comment | Vendor | Vendor URL
Bondtech BMG parts
HextrudORT_HotEnd_DRAGON | BUY | 1 |  | Bondetech mini gears 1.75/5.0 | Included in BMG Internals Set for HextrudORT | (BUY) KIT | 1 | Gear set for filament size 1.75 mm, primary gear with inner diameter 5 mm, secondary gear with two needle bearings,M3x2 setscrew and one 3 x 20 mm shaft. | Bondtech | https://www.bondtech.se/product/bmg-internals-set-for-hextrudort/
HextrudORT_HotEnd_DRAGON | BUY | 2 |  | Bondtech_Shaft_assembly | Included in BMG Internals Set for HextrudORT | (BUY) KIT | 1 | Replacement Shaft assembly for our Bondtech Mini Geared (BMG), SingleDirect and DualDirect extruders. It includes the set screw for primary 1.75/5.0 drive gear. | Bondtech | https://www.bondtech.se/product/bmg-internals-set-for-hextrudort/
HextrudORT_HotEnd_DRAGON | BUY | 3 |  | Bondtech_Thumbscrew_assembly v1 | Included in BMG Internals Set for HextrudORT | (BUY) KIT | 1 | From BMG Extruder | Bondtech | https://www.bondtech.se/product/bmg-internals-set-for-hextrudort/
HextrudORT_HotEnd_DRAGON | BUY | 4 |  | TensionArm_Pin | Included in BMG Internals Set for HextrudORT | (BUY) KIT | 1 | From BMG Extruder 3 X 20 | Bondtech | https://www.bondtech.se/product/bmg-internals-set-for-hextrudort/
HextrudORT_HotEnd_DRAGON | BUY | 5 |  | PTFE Tube Retainer | Included in BMG Internals Set for HextrudORT | (BUY) KIT | 1 | From BMG Extruder | Bondtech | https://www.bondtech.se/product/bmg-internals-set-for-hextrudort/
HextrudORT_HotEnd_DRAGON | BUY | 6a |  | OPTION A: Bearing_MR85 (from BMG) | Included in BMG Internals Set for HextrudORT | (BUY) KIT | 2* | OPTION A Use MR85 5x8x2.5 bearings from BMG *Qty1 bearing will be used in the carriage BOM. Qty 1 required in this assembly + 1 in carriage = 2 for the printer | Bondtech | https://www.bondtech.se/product/bmg-internals-set-for-hextrudort/
Dragon HextrudORT
HextrudORT_HotEnd_DRAGON | BUY | 6b |  | OPTION B: Bearing_MR95_7804K105 | Bearing 5X9X3 | BUY | 1* | OPTION B These are BIGGER bearings than the ones used in the BMG. To be used with Back Plate and cover marked with "BB"
HextrudORT_HotEnd_DRAGON | BUY | 7 |  | bltouch |  | BUY | 1
HextrudORT_HotEnd_DRAGON | MAKE | 8 |  | PTFE_Guide | Comes with BMG clones | MAKE | 1 | Make from 4mm OD PTFE tube: 1 - Using Xacto blade, create internal chamfer in one end. 2 - Cut that end into an arrow shape (try to match the angle from the HextrudORT body where the hobb gears meet. 3 - Insert into HextrudORT body and cut excess length flush.
HextrudORT_HotEnd_DRAGON | BUY | 9 |  | DRAGON HOTEND | Hight temp or Standard | BUY | 1 |  | AliExpress Phaetus | https://s.click.aliexpress.com/e/_AD0Qow https://www.phaetus.com/?page_id=15+A8
HextrudORT_HotEnd_DRAGON | HARDWARE | 9 |  | M2.5X6_CapScrew_92290A056 | Screw, Capr_M2.5 X 6mm | Buy | 3
HextrudORT_HotEnd_DRAGON | HARDWARE | 10 |  | M3_Nut_94150A325 | Nut, Hex - M3 | Buy | 2
HextrudORT_HotEnd_DRAGON | HARDWARE | 11 |  | M3X25_CapScrew_92290A124 | Screw, Cap - M3X25mm | Buy | 1
HextrudORT_HotEnd_DRAGON | HARDWARE | 12 |  | M3X20_CapScrew_92290A122 | Screw, Cap - M3X20mm | Buy | 1
HextrudORT_HotEnd_DRAGON | HARDWARE | 13 |  | M3X8_CapScrew_92290A113 | Screw, Cap - M3X8mm | Buy | 1
HextrudORT_HotEnd_DRAGON | MAKE | 10a |  | BlTouchSupport for STDHT MGN9 & MGN12 Carriage | 3D Printed | MAKE | 1* | * OPTION BlTouchSupport for STDHT MGN9 & MGN12 Carriage
HextrudORT_HotEnd_DRAGON | MAKE | 10b | To come | BLTouch support for HD9 | 3D Printed | MAKE | 1* | * OPTION BlTouchSupport for HD9 Carriage
HextrudORT_HotEnd_DRAGON | MAKE | 10c |  | BLTouch support for HD12 | 3D Printed | MAKE | 1* | * OPTION BlTouchSupport for HD12 Carriage
HextrudORT_HotEnd_DRAGON | MAKE | 11 |  | HextrudORT_DRAGON_TENSION_ARM | 3D_Printed |  | 1 | NOTE ! Make sure your printer is well calibrated, these are small and precise parts. Recommended print settings: - 0.16 Layer height - Support interface: yes - Full fan at first support interfacing layer
HextrudORT_HotEnd_DRAGON | MAKE | 12 |  | HextrudORT_COVER | 3D_Printed |  | 1 | NOTE ! For Big Bearings (MR95 5X9X2.5) use: HextrudORT_COVER_BB.STL For Bearing provided with BMG (MR85 5x8x2.5) use: HextrudORT_COVER.STL
HextrudORT_HotEnd_DRAGON | MAKE | 13 |  | HextrudORT_DRAGON_Body_V1 | 3D Printed |  | 1 | NOTE ! Make sure your printer is well calibrated, these are small and precise parts. Recommended print settings: - 0.16 Layer height - Support interface: yes - Full fan at first support interfacing layer

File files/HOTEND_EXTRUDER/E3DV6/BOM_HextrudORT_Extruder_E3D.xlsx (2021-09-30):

SubAssy | Category | Item | Thumbnail | Part Name | Part Description | Make/Buy | QTY | Comment | Vendor | Vendor URL
Bondtech BMG parts
HextrudORT_HotEnd_E3D | BUY | 1 |  | Bondetech mini gears 1.75/5.0 | Included in BMG Internals Set for HextrudORT | (BUY) KIT | 1 | Gear set for filament size 1.75 mm, primary gear with inner diameter 5 mm, secondary gear with two needle bearings,M3x2 setscrew and one 3 x 20 mm shaft. | Bondtech | https://www.bondtech.se/product/bmg-internals-set-for-hextrudort/
HextrudORT_HotEnd_E3D | BUY | 2 |  | Bondtech_Shaft_assembly | Included in BMG Internals Set for HextrudORT | (BUY) KIT | 1 | Replacement Shaft assembly for our Bondtech Mini Geared (BMG), SingleDirect and DualDirect extruders. It includes the set screw for primary 1.75/5.0 drive gear. | Bondtech | https://www.bondtech.se/product/bmg-internals-set-for-hextrudort/
HextrudORT_HotEnd_E3D | BUY | 3 |  | Bondtech_Thumbscrew_assembly v1 | Included in BMG Internals Set for HextrudORT | (BUY) KIT | 1 | From BMG Extruder | Bondtech | https://www.bondtech.se/product/bmg-internals-set-for-hextrudort/
HextrudORT_HotEnd_E3D | BUY | 4 |  | TensionArm_Pin | Included in BMG Internals Set for HextrudORT | (BUY) KIT | 1 | From BMG Extruder 3 X 20 | Bondtech | https://www.bondtech.se/product/bmg-internals-set-for-hextrudort/
HextrudORT_HotEnd_E3D | BUY | 5 |  | PTFE Tube Retainer | Included in BMG Internals Set for HextrudORT | (BUY) KIT | 1 | From BMG Extruder | Bondtech | https://www.bondtech.se/product/bmg-internals-set-for-hextrudort/
HextrudORT_HotEnd_E3D | BUY | 6a |  | OPTION A: Bearing_MR85 (from BMG) | Included in BMG Internals Set for HextrudORT | (BUY) KIT | 2* | OPTION A Use MR85 5x8x2.5 bearings from BMG *Qty1 bearing will be used in the carriage BOM. Qty 1 required in this assembly + 1 in carriage = 2 for the printer | Bondtech | https://www.bondtech.se/product/bmg-internals-set-for-hextrudort/
E3D V6 HextrudORT
HextrudORT_HotEnd_E3D | BUY | 6b |  | OPTION B: Bearing_MR95_7804K105 | Bearing 5X9X3 | BUY | 1* | OPTION B These are BIGGER bearings than the ones used in the BMG. To be used with Back Plate and cover marked with "BB"
HextrudORT_HotEnd_E3D | MAKE | 7 |  | PTFE_Guide | Comes with BMG clones Any 2mm ID PTFE will do | MAKE | 1 | Make from 4mm OD PTFE tube: 1 - Using Xacto blade, create internal chamfer in one end. 2 - Cut that end into an arrow shape (try to match the angle from the HextrudORT body where the hobb gears meet. 3 - Insert into HextrudORT body and cut to match internal length of the E3D HeatSink.
HextrudORT_HotEnd_E3D | BUY | 8 |  | E3D HeatSink | From Slice Engineering | BUY | 1 | Note: this HextrudORT config can also accomodate the Mosquito Magnum and the Mosquito Magnum +. BLTouch Bracket and Part Cooling Fan duct need to be modified to accept the Magnum +.
OptionA - E3DV6
HextrudORT_HotEnd_E3D | BUY | 9 - Option A |  | E3D V6 HotEnd | E3D or Clone | BUY | 1* | Simply use this code when checking out :) : 10offe3d | E3D-Online | https://e3d-online.com/
HextrudORT_HotEnd_E3D | MAKE | 10(A1) |  | V6 BLTouch support for: HD12 | 3D Printed | MAKE | 1* | * Select BlTouch Bracket to fit your selected HextrudORT carriage.
HextrudORT_HotEnd_E3D | MAKE | 10(A2) |  | V6 BLTouch support for: STDHT MGN9 | 3D Printed | MAKE | 1* | * Select BlTouch Bracket to fit your selected HextrudORT carriage.
HextrudORT_HotEnd_E3D | MAKE | 10(A3) |  | V6 BLTouch support for: STDHT MGN12 | 3D Printed | MAKE | 1* | * Select BlTouch Bracket to fit your selected HextrudORT carriage.
HextrudORT_HotEnd_E3D | MAKE | 10(A4) | To Come | Volcano BLTouch support for HD9 | 3D Printed | MAKE | 1* | Not Available Yet * Select BlTouch Bracket to fit your selected HextrudORT carriage.
OptionB- E3DVolcano
HextrudORT_HotEnd_E3D | BUY | 9 - Option B |  | E3D Volcano HotEnd | E3D or Clone | BUY | 1* | Simply use this code when checking out :) : 10offe3d | E3D-Online | https://e3d-online.com/
HextrudORT_HotEnd_E3D | MAKE | 10(B1) |  | Volcano BLTouch support for: HD12 | 3D Printed | MAKE | 1* | * Select BlTouch Bracket to fit your selected HextrudORT carriage.
HextrudORT_HotEnd_E3D | MAKE | 10(B2) |  | Volcano BLTouch support for: STDHT MGN9 | 3D Printed | MAKE | 1* | * Select BlTouch Bracket to fit your selected HextrudORT carriage.
HextrudORT_HotEnd_E3D | MAKE | 10(B3) |  | Volcano BLTouch support for: STDHT MGN12 | 3D Printed | MAKE | 1* | * Select BlTouch Bracket to fit your selected HextrudORT carriage.
HextrudORT_HotEnd_E3D | MAKE | 10(B4) | To come | Volcano BLTouch support for HD9 | 3D Printed | MAKE | 1* | Not Available Yet * Select BlTouch Bracket to fit your selected HextrudORT carriage.
HextrudORT_HotEnd_E3D | BUY | 10 |  | bltouch | Z Probe sensor, BL touch | BUY | 1 | Better results will be obtained with OEM AntClabs BlTouch.
HextrudORT_HotEnd_E3D | HARDWARE | 11 |  | M3_Nut_94150A325 | Nut, Hex - M3 | BUY | 5
HextrudORT_HotEnd_E3D | HARDWARE | 13 |  | M3X25_CapScrew_92290A124 | Screw, Cap - M3X25mm | BUY | 1
HextrudORT_HotEnd_E3D | HARDWARE | 14 |  | M3X20_CapScrew_92290A122 | Screw, Cap - M3X20mm | BUY | 3
HextrudORT_HotEnd_E3D | HARDWARE | 15 |  | M3X6_CapScrew_92290A111 | Screw, Cap - M3X6mm | BUY | 2
HextrudORT_HotEnd_E3D | MAKE | 16 |  | HextrudORT_TENSION_ARM | 3D_Printed | MAKE | 1 | NOTE ! Make sure your printer is well calibrated, these are small and precise parts. Recommended print settings: - 0.16 Layer height - Support interface: yes - Full fan at first support interfacing layer
HextrudORT_HotEnd_E3D | MAKE | 17 |  | HextrudORT_COVER | 3D_Printed | MAKE | 1 | NOTE ! For Big Bearings (MR95 5X9X2.5) use: HextrudORT_COVER_BB.STL For Bearing provided with BMG (MR85 5x8x2.5) use: HextrudORT_COVER.STL
HextrudORT_HotEnd_E3D | MAKE | 18 |  | HextrudORT_V6Holder | 3D_Printed | MAKE | 1
HextrudORT_HotEnd_E3D | MAKE | 19 |  | HextrudORT_BODY_MOSQUITO | 3D Printed | MAKE | 1 | NOTE ! Make sure your printer is well calibrated, these are small and precise parts. Recommended print settings: - 0.16 Layer height - Support interface: yes - Full fan at first support interfacing layer

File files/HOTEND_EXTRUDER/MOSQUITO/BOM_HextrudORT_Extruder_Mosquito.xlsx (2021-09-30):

SubAssy | Category | Item | Thumbnail | Part Name | Part Description | Make/Buy | QTY | Comment | Vendor | Vendor URL
Bondtech BMG parts
HextrudORT_HotEnd_Mosquito | BUY | 1 |  | Bondetech mini gears 1.75/5.0 | Included in BMG Internals Set for HextrudORT | (BUY) KIT | 1 | Gear set for filament size 1.75 mm, primary gear with inner diameter 5 mm, secondary gear with two needle bearings,M3x2 setscrew and one 3 x 20 mm shaft. | Bondtech | https://www.bondtech.se/product/bmg-internals-set-for-hextrudort/
HextrudORT_HotEnd_Mosquito | BUY | 2 |  | Bondtech_Shaft_assembly | Included in BMG Internals Set for HextrudORT | (BUY) KIT | 1 | Replacement Shaft assembly for our Bondtech Mini Geared (BMG), SingleDirect and DualDirect extruders. It includes the set screw for primary 1.75/5.0 drive gear. | Bondtech | https://www.bondtech.se/product/bmg-internals-set-for-hextrudort/
HextrudORT_HotEnd_Mosquito | BUY | 3 |  | Bondtech_Thumbscrew_assembly v1 | Included in BMG Internals Set for HextrudORT | (BUY) KIT | 1 | From BMG Extruder | Bondtech | https://www.bondtech.se/product/bmg-internals-set-for-hextrudort/
HextrudORT_HotEnd_Mosquito | BUY | 4 |  | TensionArm_Pin | Included in BMG Internals Set for HextrudORT | (BUY) KIT | 1 | From BMG Extruder 3 X 20 | Bondtech | https://www.bondtech.se/product/bmg-internals-set-for-hextrudort/
HextrudORT_HotEnd_Mosquito | BUY | 5 |  | PTFE Tube Retainer | Included in BMG Internals Set for HextrudORT | (BUY) KIT | 1 | From BMG Extruder | Bondtech | https://www.bondtech.se/product/bmg-internals-set-for-hextrudort/
HextrudORT_HotEnd_Mosquito | BUY | 6a |  | OPTION A: Bearing_MR85 (from BMG) | Included in BMG Internals Set for HextrudORT | (BUY) KIT | 2* | OPTION A Use MR85 5x8x2.5 bearings from BMG *Qty1 bearing will be used in the carriage BOM. Qty 1 required in this assembly + 1 in carriage = 2 for the printer | Bondtech | https://www.bondtech.se/product/bmg-internals-set-for-hextrudort/
Mosquito HextrudORT
HextrudORT_HotEnd_Mosquito | BUY | 6b |  | OPTION B: Bearing_MR95_7804K105 | Bearing 5X9X3 | BUY | 1* | OPTION B These are BIGGER bearings than the ones used in the BMG. To be used with Back Plate and cover marked with "BB"
HextrudORT_HotEnd_Mosquito | MAKE | 7 |  | PTFE_Guide | Comes with BMG clones | MAKE | 1 | Make from 4mm OD PTFE tube: 1 - Using Xacto blade, create internal chamfer in one end. 2 - Cut that end into an arrow shape (try to match the angle from the HextrudORT body where the hobb gears meet. 3 - Insert into HextrudORT body and cut to match internal length of Mosquito.
HextrudORT_HotEnd_Mosquito | BUY | 8 |  | MOSQUITO HotEnd | From Slice Engineering | BUY | 1 | Note: this HextrudORT config can also accomodate the Mosquito Magnum and the Mosquito Magnum +. BLTouch Bracket and Part Cooling Fan duct need to be modified to accept the Magnum +.
HextrudORT_HotEnd_Mosquito | BUY | 9 |  | bltouch |  | BUY | 1
HextrudORT_HotEnd_Mosquito | HARDWARE | 10 |  | M3_Nut_94150A325 | Nut, Hex - M3 | Buy | 2
HextrudORT_HotEnd_Mosquito | HARDWARE | 13 |  | M2.5X6_CapScrew_92290A056 | Screw, Cap - M2.5X6mm | BUY | 2
HextrudORT_HotEnd_Mosquito | HARDWARE | 11 |  | M3X25_CapScrew_92290A124 | Screw, Cap - M3X25mm | Buy | 1
HextrudORT_HotEnd_Mosquito | HARDWARE | 12 |  | M3X20_CapScrew_92290A122 | Screw, Cap - M3X20mm | Buy | 1
HextrudORT_HotEnd_Mosquito | HARDWARE | 13 |  | M3X8_CapScrew_92290A113 | Screw, Cap - M3X8mm | Buy | 1
HextrudORT_HotEnd_Mosquito | MAKE | 10a |  | BlTouchSupport for STDHT MGN9 & MGN12 Carriage | 3D Printed | MAKE | 1* | * OPTION BlTouchSupport for STDHT MGN9 & MGN12 Carriage
HextrudORT_HotEnd_Mosquito | MAKE | 10b | To come | BLTouch support for HD9 | 3D Printed | MAKE | 1* | * OPTION BlTouchSupport for HD9 Carriage
HextrudORT_HotEnd_Mosquito | MAKE | 10c |  | BLTouch support for HD12 | 3D Printed | MAKE | 1* | * OPTION BlTouchSupport for HD12 Carriage
HextrudORT_HotEnd_Mosquito | MAKE | 11 |  | HextrudORT_TENSION_ARM | 3D_Printed |  | 1 | NOTE ! Make sure your printer is well calibrated, these are small and precise parts. Recommended print settings: - 0.16 Layer height - Support interface: yes - Full fan at first support interfacing layer
HextrudORT_HotEnd_Mosquito | MAKE | 12 |  | HextrudORT_COVER | 3D_Printed |  | 1 | NOTE ! For Big Bearings (MR95 5X9X2.5) use: HextrudORT_COVER_BB.STL For Bearing provided with BMG (MR85 5x8x2.5) use: HextrudORT_COVER.STL
HextrudORT_HotEnd_Mosquito | MAKE | 13 |  | HextrudORT_BODY_MOSQUITO | 3D Printed |  | 1 | NOTE ! Make sure your printer is well calibrated, these are small and precise parts. Recommended print settings: - 0.16 Layer height - Support interface: yes - Full fan at first support interfacing layer

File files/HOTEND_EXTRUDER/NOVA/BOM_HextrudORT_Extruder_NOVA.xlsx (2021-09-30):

SubAssy | Category | Item | Thumbnail | Part Name | Part Description | Make/Buy | QTY | Comment | Vendor | Vendor URL
Bondtech BMG parts
HextrudORT_HotEnd_Nova | BUY | 1 |  | Bondetech mini gears 1.75/5.0 | Included in BMG Internals Set for HextrudORT | (BUY) KIT | 1 | Gear set for filament size 1.75 mm, primary gear with inner diameter 5 mm, secondary gear with two needle bearings,M3x2 setscrew and one 3 x 20 mm shaft. | Bondtech | https://www.bondtech.se/product/bmg-internals-set-for-hextrudort/
HextrudORT_HotEnd_Nova | BUY | 2 |  | Bondtech_Shaft_assembly | Included in BMG Internals Set for HextrudORT | (BUY) KIT | 1 | Replacement Shaft assembly for our Bondtech Mini Geared (BMG), SingleDirect and DualDirect extruders. It includes the set screw for primary 1.75/5.0 drive gear. | Bondtech | https://www.bondtech.se/product/bmg-internals-set-for-hextrudort/
HextrudORT_HotEnd_Nova | BUY | 3 |  | Bondtech_Thumbscrew_assembly v1 | Included in BMG Internals Set for HextrudORT | (BUY) KIT | 1 | From BMG Extruder | Bondtech | https://www.bondtech.se/product/bmg-internals-set-for-hextrudort/
HextrudORT_HotEnd_Nova | BUY | 4 |  | TensionArm_Pin | Included in BMG Internals Set for HextrudORT | (BUY) KIT | 1 | From BMG Extruder 3 X 20 | Bondtech | https://www.bondtech.se/product/bmg-internals-set-for-hextrudort/
HextrudORT_HotEnd_Nova | BUY | 5 |  | PTFE Tube Retainer | Included in BMG Internals Set for HextrudORT | (BUY) KIT | 1 | From BMG Extruder | Bondtech | https://www.bondtech.se/product/bmg-internals-set-for-hextrudort/
HextrudORT_HotEnd_Nova | BUY | 6a |  | OPTION A: Bearing_MR85 (from BMG) | Included in BMG Internals Set for HextrudORT | (BUY) KIT | 2* | OPTION A Use MR85 5x8x2.5 bearings from BMG *Qty1 bearing will be used in the carriage BOM. Qty 1 required in this assembly + 1 in carriage = 2 for the printer | Bondtech | https://www.bondtech.se/product/bmg-internals-set-for-hextrudort/
NOVA HextrudORT
HextrudORT_HotEnd_Nova | BUY | 6b |  | OPTION B: Bearing_MR95_7804K105 | Bearing 5X9X3 | BUY | 2* | OPTION B These are BIGGER bearings than the ones used in the BMG. To be used with Back Plate and cover marked with "BB"
HextrudORT_HotEnd_Nova | MAKE | 7 |  | PTFE_Guide | Comes with BMG clones | MAKE | 1 | Make from 4mm OD PTFE tube: 1 - Using Xacto blade, create internal chamfer in one end. 2 - Cut that end into an arrow shape (try to match the angle from the HextrudORT body where the hobb gears meet. 3 - Insert into HextrudORT body and cut excess length flush.
HextrudORT_HotEnd_Nova | BUY | 8 |  | NOVA HotEnd | From 3DPassion.com | BUY | 1 | BE AWARE, if using the 100W heater cartridge available for NOVA, Duet might trigger errors during PID tune due to too much overshoot (default 15C). This can be resolved by Inserting an M570 H1* T25 in your config file. * is your heater number. Klipper seems to be handling this power without any issue. HevORT Discount: Get 2 free nozzles (0.33mm and 1mm) when purchasing a Nova HotEnd kit. https://forums.hevort.com/viewtopic.php?f=18&t=504 Promo code: (Apply code at Check out) HEVORT | 3D Passion | https://3dpassion.com/nova
HextrudORT_HotEnd_Nova | BUY | 9 |  | bltouch |  | BUY | 1
HextrudORT_HotEnd_Nova | HARDWARE | 10 |  | M3_Nut_94150A325 | Nut, Hex - M3 | Buy | 2
HextrudORT_HotEnd_Nova | HARDWARE | 13 |  | M2.5X6_CapScrew_92290A056 | Screw, Cap - M2.5X6mm | BUY | 2
HextrudORT_HotEnd_Nova | HARDWARE | 11 |  | M3X25_CapScrew_92290A124 | Screw, Cap - M3X25mm | Buy | 1
HextrudORT_HotEnd_Nova | HARDWARE | 12 |  | M3X20_CapScrew_92290A122 | Screw, Cap - M3X20mm | Buy | 1
HextrudORT_HotEnd_Nova | HARDWARE | 13 |  | M3X8_CapScrew_92290A113 | Screw, Cap - M3X8mm | Buy | 1
HextrudORT_HotEnd_Nova | MAKE | 10a |  | BlTouchSupport for STDHT MGN9 & MGN12 Carriage | 3D Printed | MAKE | 1* | * OPTION BlTouchSupport for STDHT MGN9 & MGN12 Carriage
HextrudORT_HotEnd_Nova | MAKE | 10b | To come | BLTouch support for HD9 | 3D Printed | MAKE | 1* | * OPTION BlTouchSupport for HD9 Carriage
HextrudORT_HotEnd_Nova | MAKE | 10c |  | BLTouch support for HD12 | 3D Printed | MAKE | 1* | * OPTION BlTouchSupport for HD12 Carriage
HextrudORT_HotEnd_Nova | MAKE | 11 |  | HextrudORT_TENSION_ARM | 3D_Printed |  | 1 | NOTE ! Make sure your printer is well calibrated, these are small and precise parts. Recommended print settings: - 0.16 Layer height - Support interface: yes - Full fan at first support interfacing layer
HextrudORT_HotEnd_Nova | MAKE | 12 |  | HextrudORT_COVER | 3D_Printed |  | 1 | NOTE ! For Big Bearings (MR95 5X9X2.5) use: HextrudORT_COVER_BB.STL For Bearing provided with BMG (MR85 5x8x2.5) use: HextrudORT_COVER.STL
HextrudORT_HotEnd_Nova | MAKE | 13 |  | HextrudORT_BODY_NOVA | 3D Printed |  | 1 | NOTE ! Make sure your printer is well calibrated, these are small and precise parts. Recommended print settings: - 0.16 Layer height - Support interface: yes - Full fan at first support interfacing layer

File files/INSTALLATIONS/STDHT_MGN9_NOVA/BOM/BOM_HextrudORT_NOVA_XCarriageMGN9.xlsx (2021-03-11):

SubAssy | Category | Item | Thumbnail | Part Name | Part Description | Make/Buy | QTY | Comment | Vendor | Vendor URL
HextrudORT STDHT_MGN9_NOVA | BUY | 1 |  | Bondetech mini gears v1 | From BMG extruder | BUY | 1 | From BMG Extruder
HextrudORT STDHT_MGN9_NOVA | BUY | 2 |  | Bondtech_Shaft_assembly v1 | From BMG extruder | BUY | 1 | From BMG Extruder *NOTE* Short side of the shaft might need to be filed down to avoid grinding against stepper motor.
HextrudORT STDHT_MGN9_NOVA | BUY | 3 |  | Bondtech_Thumbscrew_assembly v1 | From BMG extruder | BUY | 1 | From BMG Extruder
HextrudORT STDHT_MGN9_NOVA | BUY | 4 |  | TensionArm_Pin | Make From BMG arm pin | BUY | 1 | From BMG Extruder
HextrudORT STDHT_MGN9_NOVA | BUY | 5 |  | PTFE Tube Retainer | Retainer, PTFE Tube 4mm | BUY | 1 | Is included with certain BMG clones. If not, need to purchase separately
HextrudORT STDHT_MGN9_NOVA | BUY | 6a |  | OPTION A: Bearing_MR95_7804K105 | Bearing 5X9X2.5 | BUY | 2* | OPTION A These are BIGGER bearings than the ones used in the BMG. To be used with Back Plate and cover marked with "BB"
HextrudORT STDHT_MGN9_NOVA | BUY | 6b |  | OPTION B: Bearing_MR85 (from BMG) | Bearing 5X8X2.5 | BUY | 2* | OPTION B Use MR85 5x8x2.5 bearings from BMG
HextrudORT STDHT_MGN9_NOVA | BUY | 7 |  | LDO_NEMA14_36STH17-1004AHG v6 v2 | LDO NEMA 14 Round | BUY | 1 | WARNING!! DO NOT SET CURRENT HIGHER THAN 0.400ma in your printer config file. These motors are Class H and are rated for 180C, they can become VERY HOT and might melt your carriage Spec: https://miragec79.github.io/HextrudORT/docs/LDO-36STH17-1004AHG-RevA_1.pdf
HextrudORT STDHT_MGN9_NOVA | MAKE | 8 |  | PTFE_Guide | Comes with BMG clones | MAKE | 1 | Make from 4mm OD PTFE tube: 1 - Using Xacto blade, create internal chamfer in one end. 2 - Cut that end into an arrow shape (try to match the angle from the HextrudORT body where the hobb gears meet. 3 - Insert into HextrudORT body and cut excess length flush.
HextrudORT STDHT_MGN9_NOVA | BUY | 9 |  | NOVA HotEnd | From 3DPassion.com | BUY | 1 | BE AWARE, if using the 100W heater cartridge available for NOVA, Duet might trigger errors during PID tune due to too much overshoot (default 15C). This can be resolved by Inserting an M570 H1* T25 in your config file. * is your heater number. Klipper seems to be handling this power without any issue.
HextrudORT STDHT_MGN9_NOVA | BUY | 10 |  | Opto endstop PM | Optical End-Stop | BUY | 1
HextrudORT STDHT_MGN9_NOVA | BUY | 11 |  | bltouch |  | BUY | 1
HextrudORT STDHT_MGN9_NOVA | HARDWARE | 12 |  | M2.5X4_CapScrew_92290A853 | Screw, Cap - M2.5X4mm | BUY | 1
HextrudORT STDHT_MGN9_NOVA | HARDWARE | 13 |  | M2.5X6_CapScrew_92290A056 | Screw, Cap - M2.5X6mm | BUY | 4
HextrudORT STDHT_MGN9_NOVA | HARDWARE | 14 |  | M2.5X8_CapScrew_92290A058 | Screwm Cap_M2.5 X 8mm | BUY | 1
HextrudORT STDHT_MGN9_NOVA | HARDWARE | 15 |  | M3X6_CapScrew_92290A111 v4 | Screw, Cap - M3X6mm | BUY | 3
HextrudORT STDHT_MGN9_NOVA | HARDWARE | 16 |  | M3X8_CapScrew_92290A113 v6 | Screw, Cap - M3X8mm | BUY | 1
HextrudORT STDHT_MGN9_NOVA | HARDWARE | 17 |  | M3X12_CapScrew_92290A117 | Screw, Cap - M3X12mm | BUY | 2
HextrudORT STDHT_MGN9_NOVA | HARDWARE | 18 |  | M3X14_CapScrew_92290A118 | Screw, Cap - M3X14 | BUY | 1
HextrudORT STDHT_MGN9_NOVA | HARDWARE | 19 |  | M3X16_CapScrew_92290A120 | Screw, Cap - M3X16mm | BUY | 1
HextrudORT STDHT_MGN9_NOVA | HARDWARE | 20 |  | M3X20_CapScrew_92290A122 v3 | Screw, Cap - M3X20mm | BUY | 2
HextrudORT STDHT_MGN9_NOVA | HARDWARE | 21 |  | M3X25_CapScrew_92290A124 v4 | Screw, Cap - M3X25mm | BUY | 2
HextrudORT STDHT_MGN9_NOVA | HARDWARE | 22 |  | M3X30_CapScrew_92290A126 | Screw, Cap - M3X30mm | BUY | 2
HextrudORT STDHT_MGN9_NOVA | HARDWARE | 23 |  | M3_Nut_94150A325 v4 | Nut, Hex - M3 | BUY | 10
HextrudORT STDHT_MGN9_NOVA | MAKE | 24 |  | HextrudORT_BODY_NOVA | 3D Printed | MAKE | 1 | NOTE ! Make sure your printer is well calibrated, these are small and precise parts. Recommended print settings: - 0.16 Layer height - Support interface: yes - Full fan at first support interfacing layer | Thingiverse Alternate: GitHub | https://www.thingiverse.com/thing:4786341 alternate: https://github.com/MirageC79/HextrudORT/tree/main/files/STDHT_MGN9_NOVA/STL
HextrudORT STDHT_MGN9_NOVA | MAKE | 25 |  | HextrudORT_TENSION_ARM | 3D_Printed | MAKE | 1 | NOTE ! Make sure your printer is well calibrated, these are small and precise parts. Recommended print settings: - 0.16 Layer height - Support interface: yes - Full fan at first support interfacing layer | Thingiverse Alternate: GitHub | https://www.thingiverse.com/thing:4786341 alternate: https://github.com/MirageC79/HextrudORT/tree/main/files/STDHT_MGN9_NOVA/STL
HextrudORT STDHT_MGN9_NOVA | MAKE | 26 |  | HextrudORT_COVER | 3D_Printed | MAKE | 1 | NOTE ! For Big Bearings (MR95 5X9X2.5) use: HextrudORT_COVER_BB.STL For Bearing provided with BMG (MR85 5x8x2.5) use: HextrudORT_COVER.STL | Thingiverse Alternate: GitHub | https://www.thingiverse.com/thing:4786341 alternate: https://github.com/MirageC79/HextrudORT/tree/main/files/STDHT_MGN9_NOVA/STL
HextrudORT STDHT_MGN9_NOVA | MAKE | 27 |  | CarriageBAckPlate_Body | 3D Printed | MAKE | 1 | NOTE ! For Big Bearings (MR95 5X9X2.5) use: HextrudORT_ BackPlate_STDHT_MGN9_BB.stl For Bearing provided with BMG (MR85 5x8x2.5) use: HextrudORT_ BackPlate_STDHT_MGN9.stl | Thingiverse Alternate: GitHub | https://www.thingiverse.com/thing:4786341 alternate: https://github.com/MirageC79/HextrudORT/tree/main/files/STDHT_MGN9_NOVA/STL
HextrudORT STDHT_MGN9_NOVA | MAKE | 28 |  | Carriage_Body | 3D PRinted | MAKE | 1 | NOTE ! To be used with MGN9H Rail on X cross member | Thingiverse Alternate: GitHub | https://www.thingiverse.com/thing:4786341 alternate: https://github.com/MirageC79/HextrudORT/tree/main/files/STDHT_MGN9_NOVA/STL
HextrudORT STDHT_MGN9_NOVA | MAKE | 29 |  | TensionnerBLock | 3D Printed | MAKE | 2 | NOTE ! Make sure your printer is well calibrated, these are small and precise parts. Recommended print settings: - 0.16 Layer height - Support interface: yes - Full fan at first support interfacing layer | Thingiverse Alternate: GitHub | https://www.thingiverse.com/thing:4786341 alternate: https://github.com/MirageC79/HextrudORT/tree/main/files/STDHT_MGN9_NOVA/STL
HextrudORT STDHT_MGN9_NOVA | MAKE | 30 |  | OpticalSupport_Body | 3D Printed | MAKE | 1 |  | Thingiverse Alternate: GitHub | https://www.thingiverse.com/thing:4786341 alternate: https://github.com/MirageC79/HextrudORT/tree/main/files/STDHT_MGN9_NOVA/STL
HextrudORT STDHT_MGN9_NOVA | MAKE | 31 |  | BlTouchSupport | 3D Printed | MAKE | 1 |  | Thingiverse Alternate: GitHub | https://www.thingiverse.com/thing:4786341 alternate: https://github.com/MirageC79/HextrudORT/tree/main/files/STDHT_MGN9_NOVA/STL
HextrudORT STDHT_MGN9_NOVA | MAKE | 32 |  | NovaBottomBrace_Body | 3D Printed | MAKE | 1 | To be made from Printed Circuit Board (1.6mm thk) DIY material. Install copper side against Heat Sink. | Thingiverse Alternate: GitHub | https://www.thingiverse.com/thing:4786341 alternate: https://github.com/MirageC79/HextrudORT/tree/main/files/STDHT_MGN9_NOVA/STL

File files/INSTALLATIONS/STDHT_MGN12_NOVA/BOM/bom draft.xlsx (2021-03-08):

Item # | Thumbnail | Part Name | Description | Make/Buy | Quantity | Vendor | Vendor URL
1 |  | HextrudORT_COVER | 3D_Printed |  | 1
2 |  | HextrudORT_TENSION_ARM | 3D_Printed |  | 1
3 |  | Bondtech_Shaft_assembly v1 | From BMG extruder |  | 1
4 |  | Bondetech mini gears v1 | From BMG extruder |  | 1
5 |  | Bondtech_Thumbscrew_assembly v1 | From BMG extruder |  | 1
6 |  | LDO_NEMA14_36STH17-1004AHG v6 v2 | LDO NEMA 14 Round |  | 1
7 |  | Bearing_MR95_7804K105 | Bearing 5X9X2.5 |  | 2
8 |  | M3X25_CapScrew_92290A124 v4 | Screw, Cap - M3X25mm | Buy | 1
9 |  | M3X8_CapScrew_92290A113 v6 | Screw, Cap - M3X8mm | Buy | 1
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

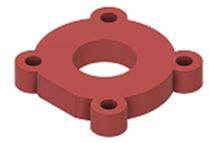
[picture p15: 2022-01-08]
files/HOTEND_EXTRUDER/RAPIDO/BOM_HextrudORT_Extruder_Rapido_files/BOM_HextrudORT_Extruder_Dragon_24158_image051.png

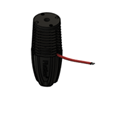
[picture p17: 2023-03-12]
files/HOTEND_EXTRUDER/RAPIDO/BOM_HextrudORT_Extruder_Rapido_files/BOM_HextrudORT_Extruder_Dragon_24158_image022.png

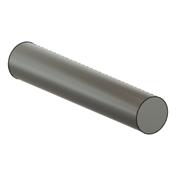
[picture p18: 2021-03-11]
files/HOTEND_EXTRUDER/RAPIDO/BOM_HextrudORT_Extruder_Rapido_files/BOM_HextrudORT_Extruder_Dragon_24158_image009.png

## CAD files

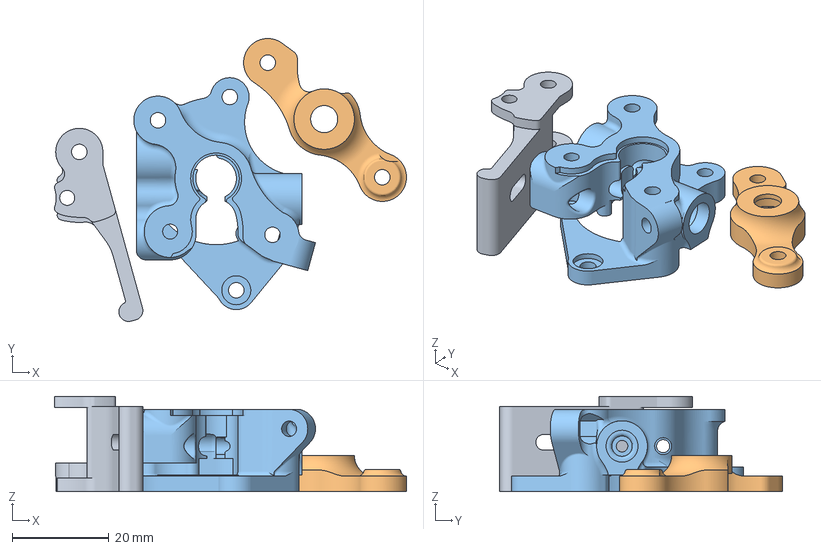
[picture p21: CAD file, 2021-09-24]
docs/PRINT_SETTINGS/HextrudORT_BODY_NOVA_V2.3mf
72.8 x 58.5 x 19.7 mm
HextrudORT_TENSION_ARM_NOVAV2.stl
HextrudORT_COVER_BB_V1.stl
HextrudORT_BODY_NOVA_V2.stl

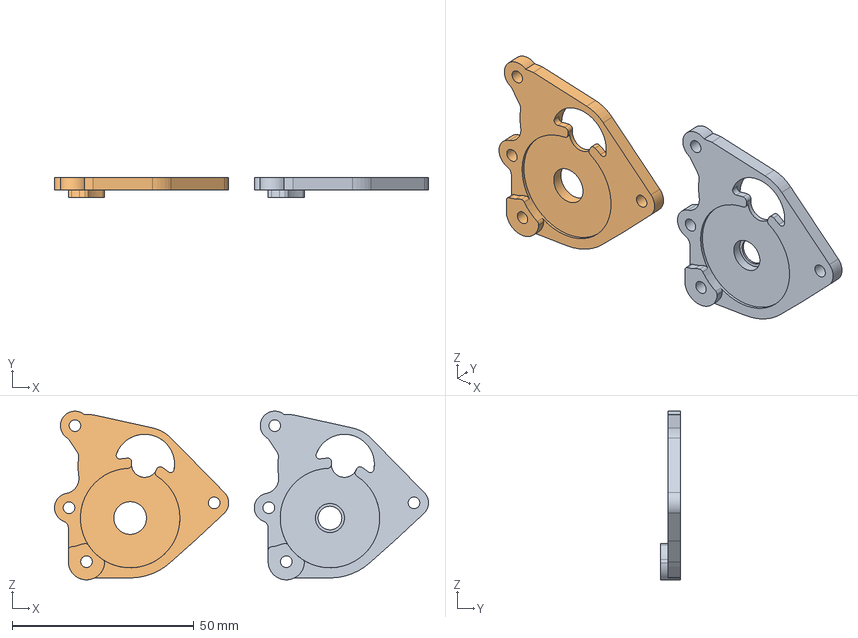
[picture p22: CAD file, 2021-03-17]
files/CARRIAGE/BLANK/Combo Cad v2.step
103.0 x 5.50 x 46.4 mm
HextrudORT_BLANK_CarriageBackPlate_Body
HextrudORT_BLANK_CarriageBackPlate_Body_BB_V1

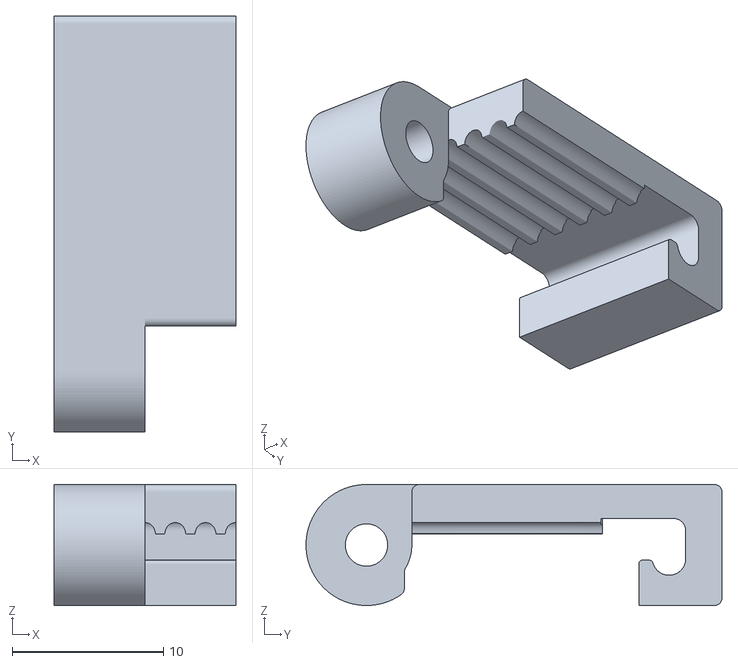
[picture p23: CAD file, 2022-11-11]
files/CARRIAGE/HD12/STL/HD12BeltLockFRLH_Back.stl
12.0 x 27.5 x 8.00

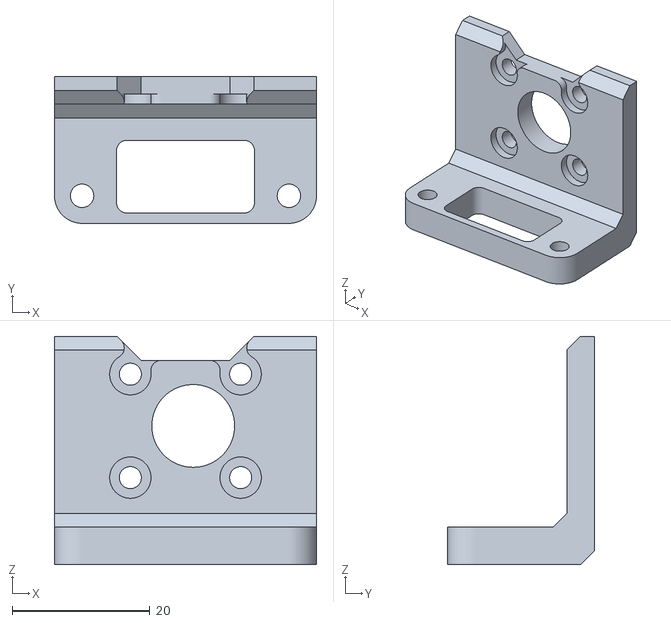
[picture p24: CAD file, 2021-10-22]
files/CARRIAGE/HD12/STL/MGN9/Cooling/HD12_MGN12_NOVA_EVA_Bracket_Nova v1.stl
38.0 x 21.3 x 33.1

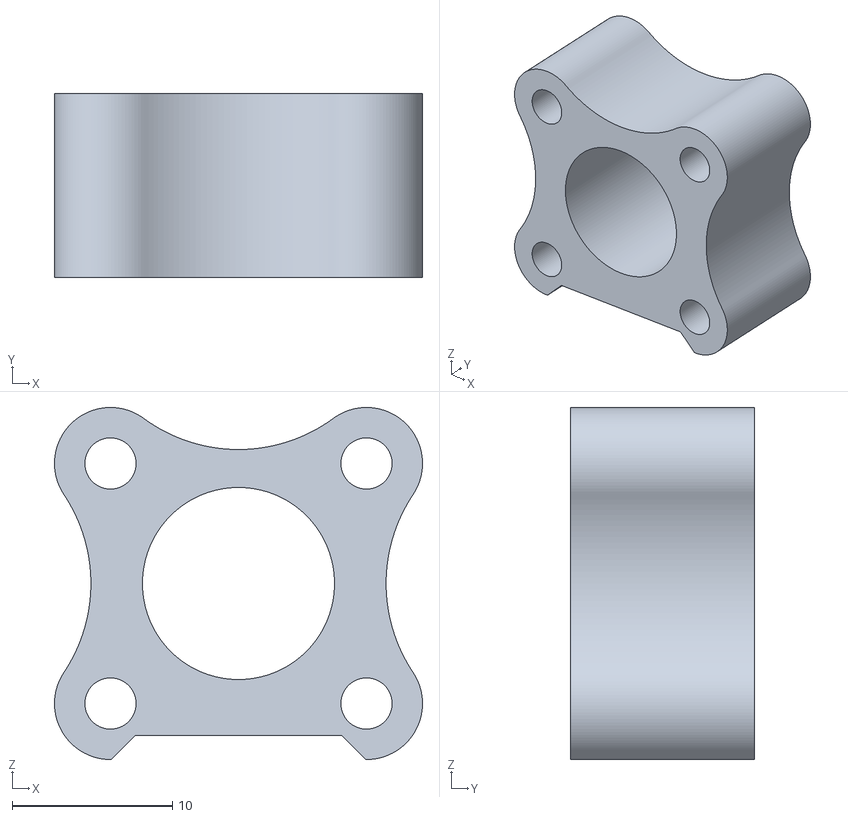
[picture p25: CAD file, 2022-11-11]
files/CARRIAGE/HD12/STL/MGN9/HD12_MGN9ReInforced_HortPC_SpacerVolcano.stl
23.0 x 11.5 x 22.0

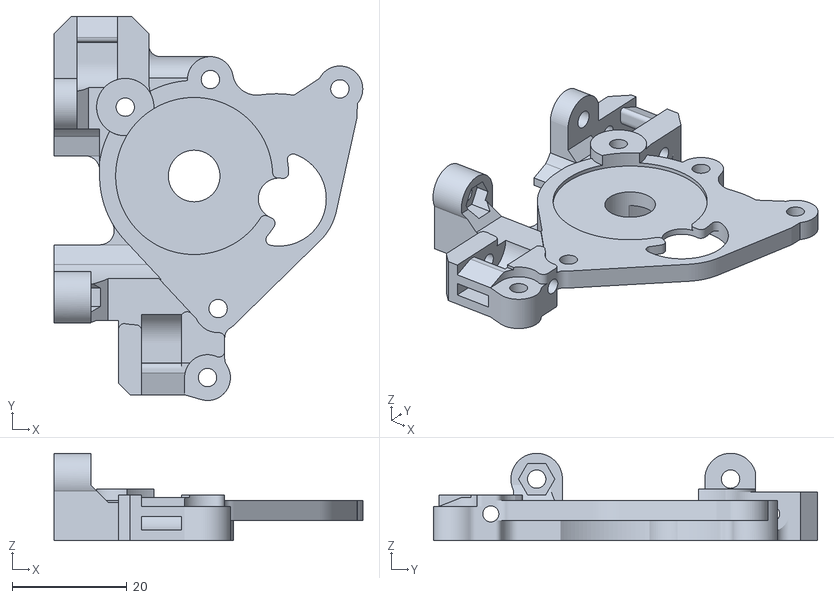
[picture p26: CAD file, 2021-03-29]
files/CARRIAGE/STDHT_MGN12/STL/HextrudORT_STDHT_MGN12_CarriageBackPlate_Body_BB_V1.stl
53.8 x 67.0 x 15.2

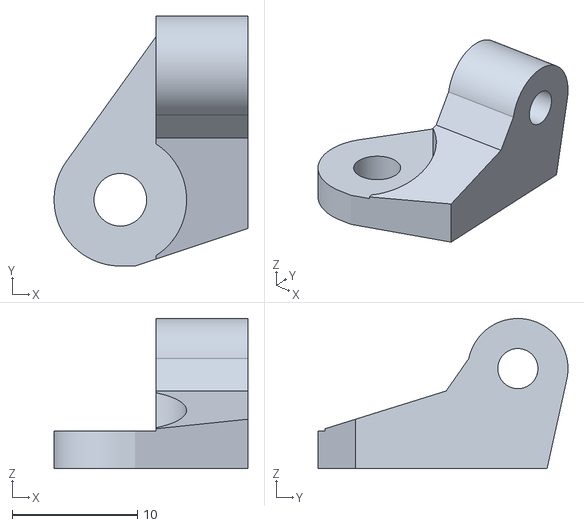
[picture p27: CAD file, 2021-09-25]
files/COOLING/EVA/HD12_Nova_EVA_UpperFanSupport.stl
15.5 x 20.0 x 12.0

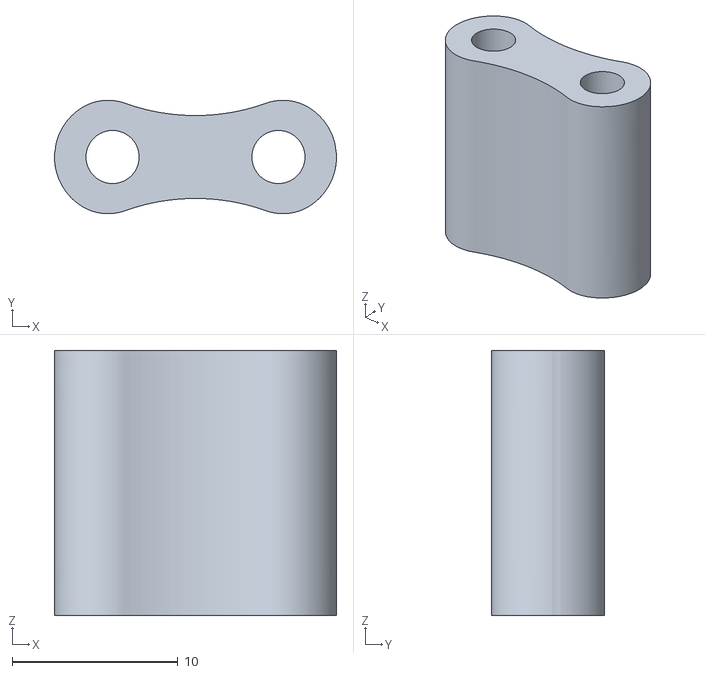
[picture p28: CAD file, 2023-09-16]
files/COOLING/TENTACOOL/HDx_VZPrintHead_TentacoolSpacer_GoliathLong.stl
17.0 x 6.84 x 16.0

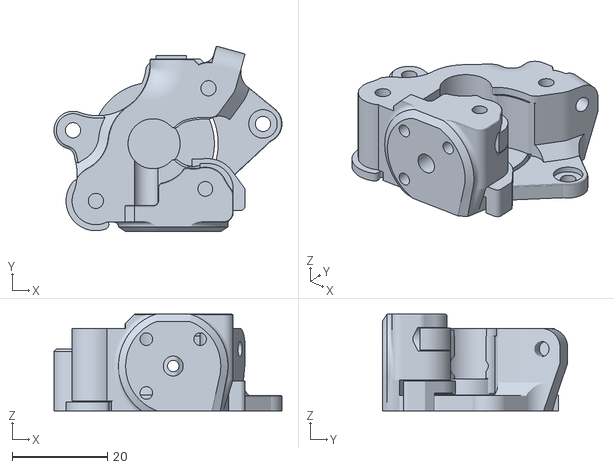
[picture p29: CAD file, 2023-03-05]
files/HOTEND_EXTRUDER/DRAGON/STL/HextrudORT_Dragon_Rapido_body_V1.6_RIDGA_Supported.stl
48.0 x 39.0 x 20.3

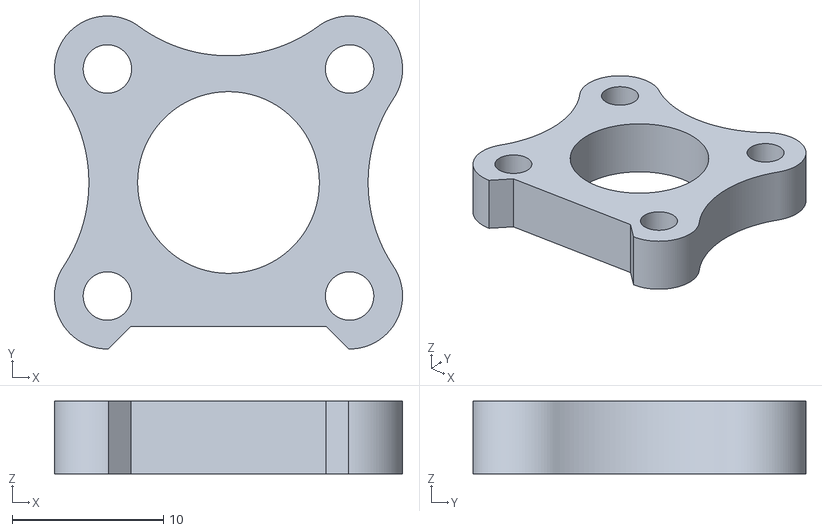
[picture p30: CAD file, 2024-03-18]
files/HOTEND_EXTRUDER/E3DV6/STL/Tentacool_Spacer_HD12_MGN9_V6.stl
23.0 x 22.0 x 4.80

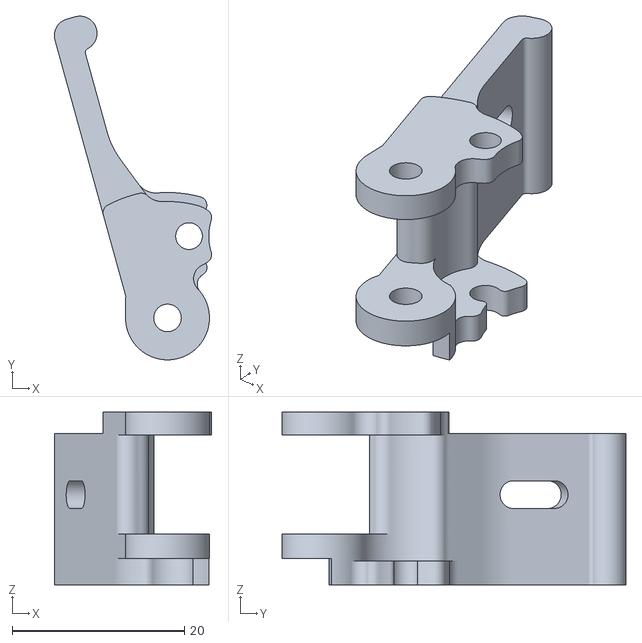
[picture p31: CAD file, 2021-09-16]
files/HOTEND_EXTRUDER/MOSQUITO/STL/HextrudORT_TENSION_ARM_V1.1.stl
18.3 x 39.9 x 20.1

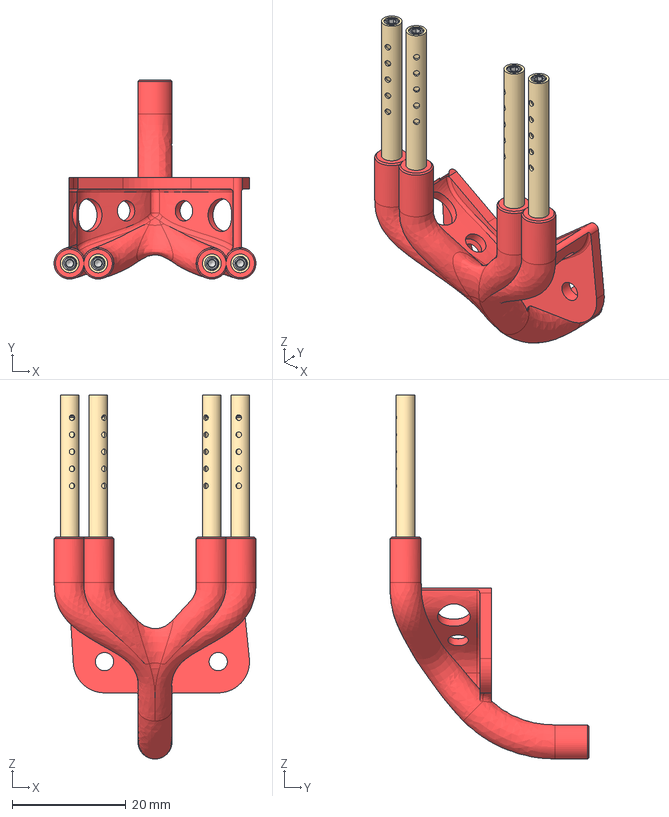
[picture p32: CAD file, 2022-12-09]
files/HOTEND_EXTRUDER/NOVA/STL/HextrudORT_ NOVA_BerdAIR_Quad_NOVAHD12_MGN12.step
35.5 x 35.0 x 64.0 mm
BerdAIR_NOVA_HD12_Manifold
M2.5X4_GrubScrew_92605A064 x 4
BerdAirTube x 4

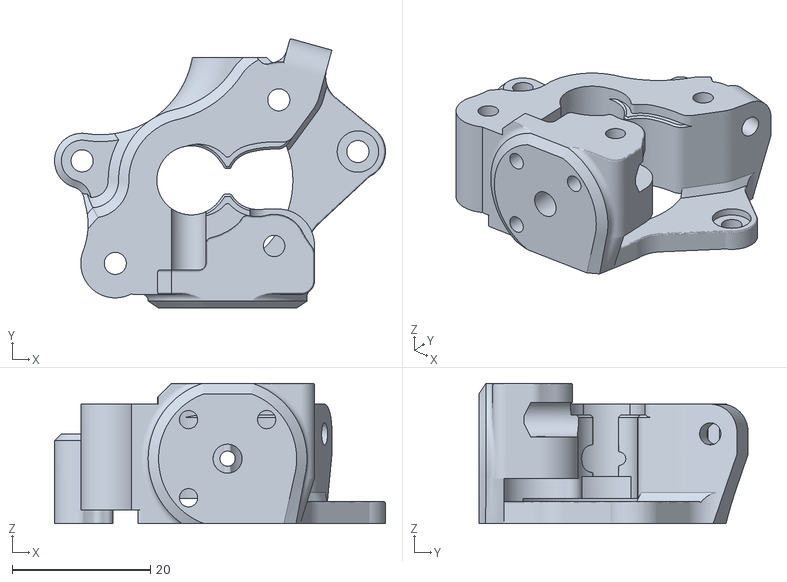
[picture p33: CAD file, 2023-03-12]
files/HOTEND_EXTRUDER/RAPIDO/STLs/HextrudORT_Dragon_Rapido_body_V1.65_RIDGA.stl
48.0 x 39.0 x 20.3

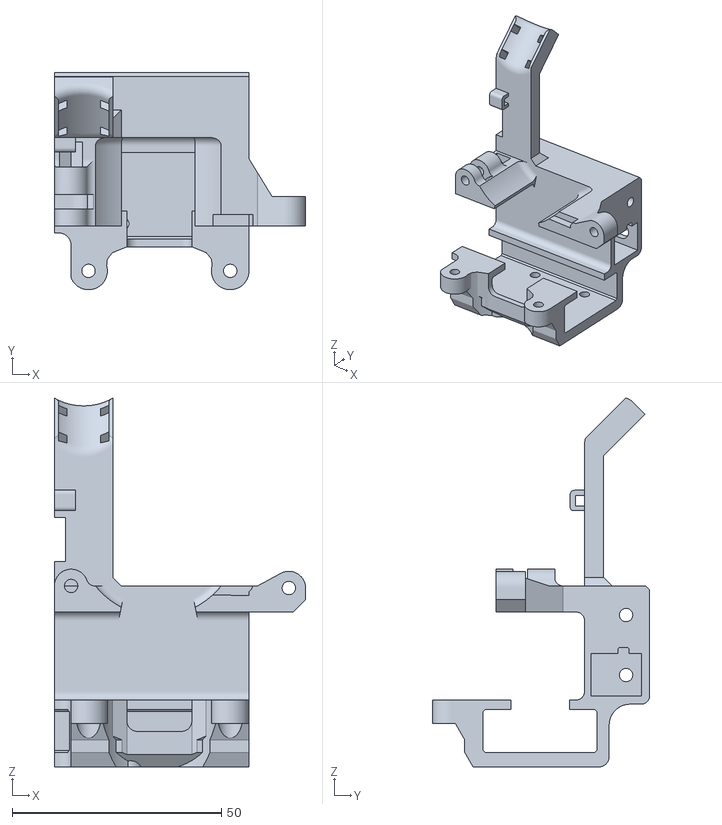
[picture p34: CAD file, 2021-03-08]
files/INSTALLATIONS/STDHT_MGN12_NOVA/STL/HextrudORT_Carriage_STDHT_MGN12.stl
60.0 x 51.9 x 88.1

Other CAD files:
files/INSTALLATIONS/STDHT_MGN9_NOVA/STL/HextrudORT_Carriage_STDHT_MGN9.stl
files/CARRIAGE/BLANK/HextrudORT_BLANK_CarriageBackPlate_Body_V1.stl
files/CARRIAGE/HD12/STL/HD12BeltLockFRLH_Front.stl
files/CARRIAGE/HD12/STL/MGN9/Cooling/EVA_Duct v2.1 Straight v1.stl
files/CARRIAGE/BLANK/HextrudORT_BLANK_CarriageBackPlate_Body_BB_V1.stl
files/CARRIAGE/HD12/STL/Archives/HextrudORT_HD12_CarriageBackPlate_Body_V1.stl
files/CARRIAGE/HD12/STL/HextrudORT3.1_HD12_Carriage_Body_BB_V1.stl
files/CARRIAGE/HD12/STL/HextrudORT_CarriageBackPlate_Body.stl
files/CARRIAGE/HD12/STL/HextrudORT_HD12_CarriageBackPlate_Body_BB_V1.5.stl
files/CARRIAGE/HD12/STL/HextrudORT_HD12_CarriageBackPlate_Body_BB_V1.stl
files/CARRIAGE/HD12/STL/HextrudORT_HD12_CarriageBackPlate_Body_V1.1.stl
files/CARRIAGE/HD12/STL/HextrudORT_HD12_Carriage_Body_V1.stl
files/CARRIAGE/HD12/STL/HextrudORT_HD12_OpticalSupport_Body_V1.stl
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

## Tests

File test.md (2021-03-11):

<iframe src="https://hotmail114573.autodesk360.com/shares/public/SH56a43QTfd62c1cd968596545b921c6c093?mode=embed" width="800" height="600" allowfullscreen="true" webkitallowfullscreen="true" mozallowfullscreen="true"  frameborder="0"></iframe>

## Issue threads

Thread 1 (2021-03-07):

Report issues by creating a new entry here

MirageC79, 2021-03-07:

SimpleSafeName, 2022-02-05:
Not really a bug, but still a good place to submit this.

1) I remixed both of the duct files to include external supports for printing without support. Printing with supports didn't work for me. Ugly, but effective.

2) The "HextrudORT_Dragon_TENSION_ARM_body_V1.5_With_Support.stl" file wouldn't come apart and I ended up destroying the part to get it out. So I remixed it with tubes for support.

3) The "HextrudORT_Dragon_Rapido_body_V1.5_With_Support.stl" nearly wouldn't come apart, but in the end it did. Are there recommended slicer settings for these parts?

[Dragon Rapido Parts.zip](https://github.com/MirageC79/HextrudORT/files/8009000/Dragon.Rapido.Parts.zip)
?

kozross, 2023-06-05:
Not an issue as much as a question: what are the dimensions of the HextrudORT, specifically the extruder part? I couldn't find a CAD model I could measure, and I'd like to know what the dimensions of it are for a project I plan to work on.

onlineapps-cloud, 2024-03-10:
hi, in web documentation i found 2 broken links
https://docs.hevort.com/bom/BOM_Electronics.htm
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
seems that vendor change product link.

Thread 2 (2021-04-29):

Tolerances to tight around the BMG gears?

Megamannen, 2021-04-29:
My calibration isn't perfect, but it's quite good. And the BMG-gear on the tensioning arm (HextrudORT_Dragon_TENSION_ARM_body_V1.stl) is scraping the inside of HextrudORT_Dragon_body_V1.stl

Is there a reason why it needs to be that tight of a tolerence?

Closed 2021-11-23.

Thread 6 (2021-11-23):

Dragon cad link not working.

hamm3rs, 2021-11-23:
HextrudORT dragon cad link opens in the fusion app thing a ma bob but gets stuck at step 2 of 3 and wont load model.

MirageC79, 2021-11-23:
I just re-saved it and it seams to work now.  Let me know if it works.
https://a360.co/3tqIMhf

hamm3rs, 2021-11-25:
Working

Thanks.

MirageC79, 2021-12-30:
Cool!  Closing the issue.

Closed 2021-12-30.

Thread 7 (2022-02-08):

Extra parts in object browser

SimpleSafeName, 2022-02-08:
In the HextrudORT_Rapido_Installation (https://hotmail114573.autodesk360.com/g/shares/SH9285eQTcf875d3c53938c46624cd645c79)

the parts that are included with the arm and body to make the printing easier, and then to be disposed of, are showing up in the model.

Affected items are the:
HextrudORT_Dragon_Rapido_Body_V1.5
HextrudORT_Dragon_TENSION_ARM_body_V1.5

The extra parts show up in my browser as gold parts, and can be hidden.

MirageC79, 2022-05-26:
These parts are supports, 2 types of STL files were created. With or without these pre-made supports.
you can hide them from the design view tree to facilitate visualization.

Closed 2022-05-26.

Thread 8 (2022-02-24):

Links to Thingiverse are messed up

FRUCHTiii, 2022-02-24:
Within the BOM of Rapido HextrudORT the links to Thingiverse are pointing to complete different parts.

For Examle:
HextrudORT_DRAGON_RAPIDO TENSION_ARM_V1.5 -> Thingiverse Link https://www.thingiverse.com/thing:5173659 -> Shows up a Headphone holder

MirageC79, 2022-05-26:
Thank you for letting me know.
I have corrected the links to both Thingiverse and GitHub for all available carriages into their respective BOM.

Closed 2022-05-26.

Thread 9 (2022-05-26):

Collision

Kazathor, 2022-05-26:
Collision issue with nema 14 motor in 2020 rail. Requires 2-3mm filing.

MirageC79, 2022-05-26:
Thanks for reporting this.  Are you using Carbon Fiber tube or 2020 Aluminum Extrusion?  CF tubes are usually a bit larger (20.3mm).  Depending on the Nema14 motor brand used, some filling may be required yes.  Will add a note in the BOM for now as a redesign implicates too many changes at this point.

Kazathor, 2022-05-26:
I am using a 2020 aluminum profile. Not really a change necessary. I think a simple note that a slight filing will be necessary in some cases. The outer diameter of my motor is 36.6 mm

<a href="https://imgbb.com/">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</a>

MirageC79, 2022-05-26:
Another potential cause could be the rail.  are you using Hiwin / MGN rails?  other brands could have the carriage sitting further away from the rail seating surface therefore pulling the motor down towards the 2020 cross member in our application.

MirageC79, 2022-05-26:
The following note has been added to the BOM file for each available HextrudORT Carriages:

**Important Note:** ref: https://github.com/MirageC79/HextrudORT/issues/9
_Depending on source of components for your build, printing tolerances and the fact that the design clearances are reduced to a minimal, you may need to file/trim a section of the Nema 14 motor to clear the XY cross member.
This modification will not affect motor performance or reliability._

Issue is considered closed.

Kazathor, 2022-05-26:
> Another potential cause could be the rail. are you using Hiwin / MGN rails? other brands could have the carriage sitting further away from the rail seating surface therefore pulling the motor down towards the 2020 cross member in our application.

I use MGN12H (measured at 8mm)

Closed 2022-05-26.

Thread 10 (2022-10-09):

Carriage for HD9 missing?

finalstage, 2022-10-09:
Any chance to add a carriage for the HD9 setup? Isn't it only reducing the pulley height of the HD12 version?

Thanks a lot, loving your project.

Closed 2022-10-26.

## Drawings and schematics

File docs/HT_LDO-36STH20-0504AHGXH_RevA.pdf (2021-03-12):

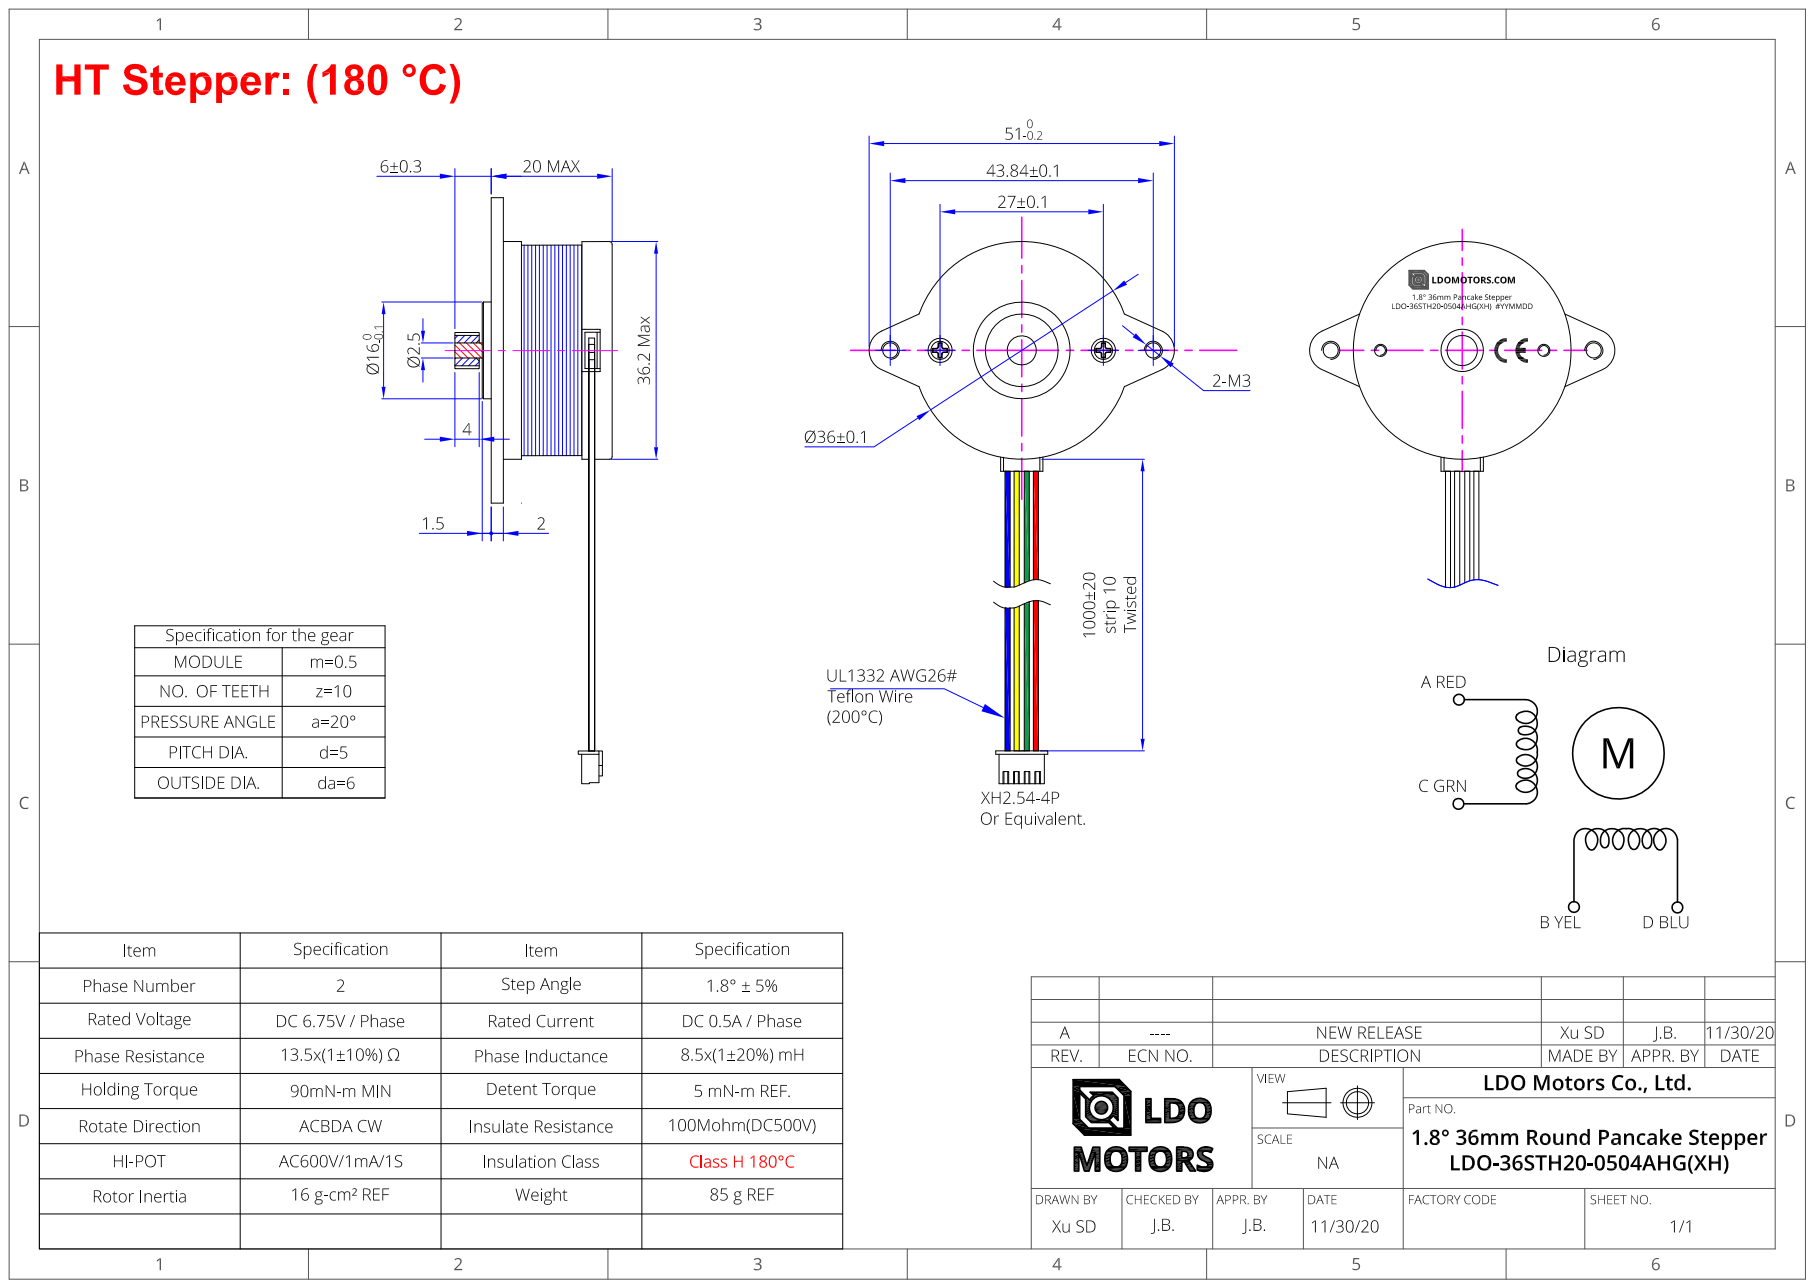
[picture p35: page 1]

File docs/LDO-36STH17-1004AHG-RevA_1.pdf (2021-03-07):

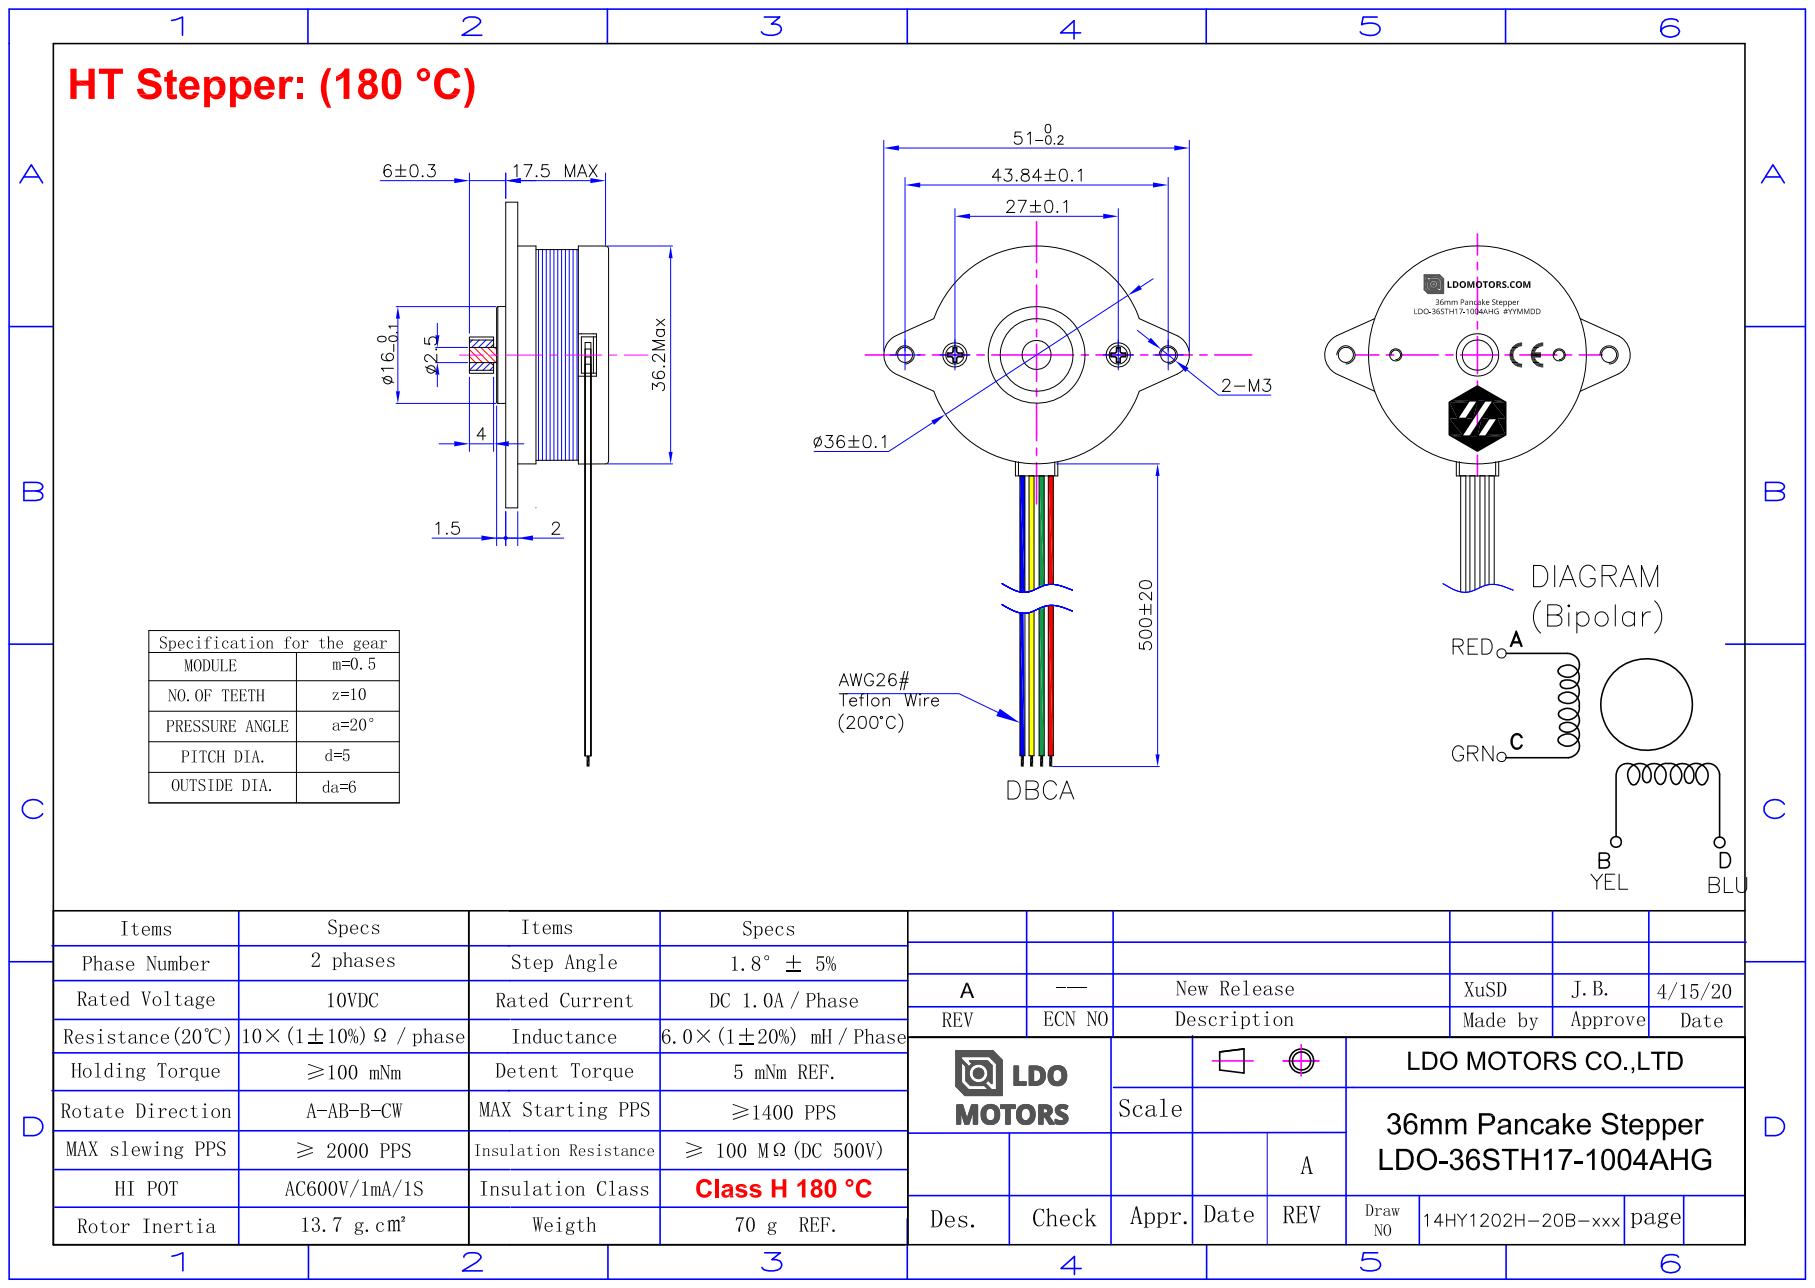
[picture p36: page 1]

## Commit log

2021-03-07 Nova STDHT mgn9 added
    [HextrudORT_ BackPlate_STDHT_MGN9.stl, HextrudORT_ BackPlate_STDHT_MGN9_BB.stl, HextrudORT_BLTouchSupport_STDHT_MGN9_NOVA.stl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]
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2021-03-07 bom excel added
    [BOM_HextrudORT_NOVA_XCarriageMGN9.xlsx]
2021-03-07 bearings from BMG
    [BOM_HextrudORT_NOVA_XCarriageMGN9.xlsx]
2021-03-08 Added STDHT MGN12
    [BOM_HextrudORT_NOVA_XCarriageMGN12.xlsx, HextrudORT_ BackPlate_STDHT_MGN12.stl, HextrudORT_ BackPlate_STDHT_MGN12_BB.stl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]
2021-03-10 ConfigTable update
    [ConfigTable.xlsx]
2021-03-11 HD12 HextrudORT Carriage
    [BOM_HextrudORT_Carriage_HD12.xlsx, BOM_HextrudORT_NOVA_XCarriageMGN9.xlsx, HextrudORTCarriage_Body.stl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]
2021-03-13 stdht mgn9
    [HextrudORT_STDHT_MGN9_CarriageBackPlate_Body_ v3.stl, HextrudORT_STDHT_MGN9_CarriageBackPlate_Body_BB v3.stl, HextrudORT_STDHT_MGN9_Carriage_Body v5.stl]
2021-03-16 V1.1 changes
    [BOM_HextrudORT_Carriage_HD12.xlsx, BOM_HextrudORT_Carriage_STDHT_MGN9.xlsx, BOM_HextrudORT_Extruder_NOVA.xlsx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]
2021-03-16 Dragon HotEnd Added
    [HextrudORT_COVER_BB_V1.stl, HextrudORT_COVER_V1.1.stl, HextrudORT_Dragon_TENSION_ARM_body_V1.stl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]
2021-03-16 Bom Dragon
    [BOM_HextrudORT_Extruder_Dragon.xlsx]
2021-03-17 Blank plate
    [HextrudORT_BLANK_CarriageBackPlate_Body_BB_V1.stl, HextrudORT_BLANK_CarriageBackPlate_Body_V1.stl, HextrudORT_COVER_V1.1.stl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]
2021-03-17 Bom Update
    [BOM_HextrudORT_Extruder_NOVA.xlsx, Combo Cad v2.step]
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2021-03-29 stdht mgn12 file relocated
    [BOM_HextrudORT_Carriage_STDHT_MGN12.xlsx, HextrudORT_STDHT_MGN12_CarriageBackPlate_Body_BB_V1.stl, HextrudORT_STDHT_MGN12_CarriageBackPlate_Body_V1.stl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]
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2021-09-05 QuadPipe Nova STD/HT MGN12 Added
    [Gear Ratio.xlsx, HD12_HexTrudORT_E3DV6_BLTouchMount.stl, HD12_HexTrudORT_E3DVolcano_BLTouchMount.stl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]
2021-09-10 Create HextrudORT_HD12_CarriageBackPlate_Body_BB_V1.5.stl
    Added a backplate version for Big Bearing without gear guard
    [HextrudORT_HD12_CarriageBackPlate_Body_BB_V1.5.stl]
2021-09-15 HextrudORT for Mosquito
    Initial release
    [BOM_HextrudORT_Extruder_Mosquito.xlsx, HextrudORT Mosquito_Body_V1.stl, HextrudORT_COVER_BB_V1.stl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]
2021-09-16 Mosquito Lever Arm V1.1 - Increased clearance
    [HextrudORT_TENSION_ARM_V1.1.stl, HextrudORT_TENSION_ARM_V1.stl]
2021-09-21 EVA Cooling solution Added for Nova HD12
    [EVA_Duct v2.1 Straight (1) v1.stl, HD12_EVA_FANDuct.stl, HD12_MGN12_NOVA_EVA_Bracket.stl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]
2021-09-22 HextrudORT for E3D release
    [BOM_HextrudORT_Extruder_E3D.xlsx, BOM_HextrudORT_Extruder_Mosquito.xlsx, HD12_E3D_V6_BLTMount_V1.stl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]
2021-09-22 E3d Logo fixed
    [HextrudORT_E3D_Body_V1.stl]
2021-09-23 Nova V2 HextrudORT files added
    [HextrudORT_TENSION_ARM_NOVAV2.stl]
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2021-09-24 HextrudORT Nova New Heatsink
    [HextrudORT_BODY_NOVA_V2.3mf, HextrudORT_BODY_NOVA_V2.stl]
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2021-09-27 BMG gear to be 3mm
    [BOM_HextrudORT_Extruder_Dragon.xlsx, BOM_HextrudORT_Extruder_E3D.xlsx, BOM_HextrudORT_Extruder_Mosquito.xlsx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]
2021-09-29 Bondtech BMG part details
    [BOM_HextrudORT_Extruder_Dragon.xlsx, BOM_HextrudORT_Extruder_E3D.xlsx, BOM_HextrudORT_Extruder_Mosquito.xlsx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]
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2021-09-29 BOm link correction
    [BOM_HextrudORT_Extruder_NOVA.xlsx]
2021-09-29 Bom Format correction
    [BOM_HextrudORT_Extruder_NOVA.xlsx]
2021-09-30 Bondtech Kit reference added
    [BOM_HextrudORT_Extruder_Dragon.xlsx, BOM_HextrudORT_Extruder_E3D.xlsx, BOM_HextrudORT_Extruder_Mosquito.xlsx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]
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2021-12-24 STL oriented for print
    [HextrudORT_Dragon_Rapido_Bowden Adapter.stl, HextrudORT_Dragon_Rapido_body_V1.5.stl, HextrudORT_Dragon_Rapido_body_V1.5_With_Support.stl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]
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2021-12-31 Create HextrudORT_HD12_MGN9_Carriage_Body v3.stl
    Thicker Wire post. Revised TieWrap provision
    [HextrudORT_HD12_MGN9_Carriage_Body v3.stl]
2022-01-08 Rapido HD12 MGN12 parts added
    [HextrudORT_Dragon_Rapido_body_V1.5_With_Support.stl, HextrudORT_HD12_MGN12_Rapido_HORTPC_UHF_Spacer v1.stl, HextrudORT_HD12_MGN12_Rapido_StructFanShroud_25mm v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]
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2022-01-08 BOM addition of User Mod for HD12 MGN12
    [BOM_HextrudORT_Extruder_Rapido.xlsx]
2022-01-08 Link to Thingiverse Added to BOM
    [BOM_HextrudORT_Extruder_Rapido.xlsx]
2022-05-26 Note added to carriages BOM
    Clearance issue might occur between Nema14 motor and X cross Member.
    Ref: https://github.com/MirageC79/HextrudORT/issues/9
    [BOM_HextrudORT_Carriage_HD12.xlsx, BOM_HextrudORT_Carriage_STDHT_MGN12.xlsx, BOM_HextrudORT_Carriage_STDHT_MGN9.xlsx]
2022-05-26 Corrected Thingiverse and GitHub links
    [BOM_HextrudORT_Carriage_HD12.xlsx, BOM_HextrudORT_Carriage_STDHT_MGN12.xlsx, BOM_HextrudORT_Carriage_STDHT_MGN9.xlsx]
2022-06-26 Minor change to increase robustness
    - Increased thickness of lower carriage mounting tabs.
    - Increased clearance for M3 nuts.
    [HextrudORT_HD12_MGN9_CarriageBAckPlate_Body_BB_V1.stl, HextrudORT_HD12_MGN9_CarriageBAckPlate_Body_BB_V3.stl, HextrudORT_HD12_MGN9_CarriageBAckPlate_Body_V1.st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]
2022-06-26 Minor changes to increase robustness
    - Better tolerance on the seating area for HextrudORT back plate
    - Added material to umbilical support for more rigidity
    [HextrudORT_HD12_MGN9_Carriage_Body v3.1.stl, HextrudORT_HD12_MGN9_Carriage_Body v3.stl]
2022-09-08 Added NF Cannon from Mellow
    [Gear Ratio.xlsx]
2022-09-08 Create HD12_E3DV6_BLTMount_HD12V6_HORTPC.stl
    Shifted to the right to allow clearance with HORTPC duct
    [HD12_E3DV6_BLTMount_HD12V6_HORTPC.stl]
2022-09-08 Create HD12MGN9_V6_HORTPC_Spacer v1.stl
    Spacer to allow use of Rapido HextrudORT HORTPC duct on E3DV6
    [HD12MGN9_V6_HORTPC_Spacer v1.stl]
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2022-11-11 Rapido UHF Duct and FanShroud BLtouch
    [HextrudORT_STDHT_MGN9_RapidoUHF_StructFanShroud_25mm_BLTouch v1.stl]
2022-11-11 HD12 Reinforced
    [HExtrudORT_HD12_MGN9_BackPlate_ReInforced.stl, HextrudORT_HD12_MGN9_Carriage_ReInforced.stl]
2022-11-11 BeltLock_Beta
    These locks will consume X print area as they are contacting with Y carriage.
    [HD12BeltLockFRLH_Back.stl, HD12BeltLockFRLH_Front.stl]
2022-11-11 E3D Structural Fan Shroud with BLtouch Volcano
    [E3DV6_StructuralFanShroud_HD12MGN9_BLT_Volcano.stl, E3D_V6_StructuralFanShroud_HD12MGN9.stl]
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2022-11-11 PrintOrientation Corrected
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2022-11-19 HD12 MGN12 Dragon EVA5015
    [EVA_Duct v2.1 Straight v1 v6.stl, HextrudORT_HD12_MGN12_DRAGON_EVA_5015Bracket.stl, HextrudORT_HD12_MGN12_EVA_FANDuct v1.stl]
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2023-03-06 V1.6 RIDGA_ Dragon Rapido
    [HextrudORT_COVER_BB_V1.stl, HextrudORT_COVER_MR84_V1.6_RIDGA.stl, HextrudORT_COVER_V1.1.stl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]
2023-03-13 Rapido 1.65 BOM Update
    [BOM_HextrudORT_Extruder_Rapido.xlsx]
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2023-08-18 Update README.md
    Include VZ print head Goliath Short
2024-03-18 Added HextrudORT Tentacool duct and spacer for HD12 MGN 9
    [Tentacool_Spacer_HD12_MGN9_V6.stl]

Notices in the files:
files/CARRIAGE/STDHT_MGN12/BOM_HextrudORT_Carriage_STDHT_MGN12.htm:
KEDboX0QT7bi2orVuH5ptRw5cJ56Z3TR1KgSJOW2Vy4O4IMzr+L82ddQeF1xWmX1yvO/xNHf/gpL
